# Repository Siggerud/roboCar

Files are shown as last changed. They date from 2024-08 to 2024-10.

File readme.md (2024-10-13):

# Robocar
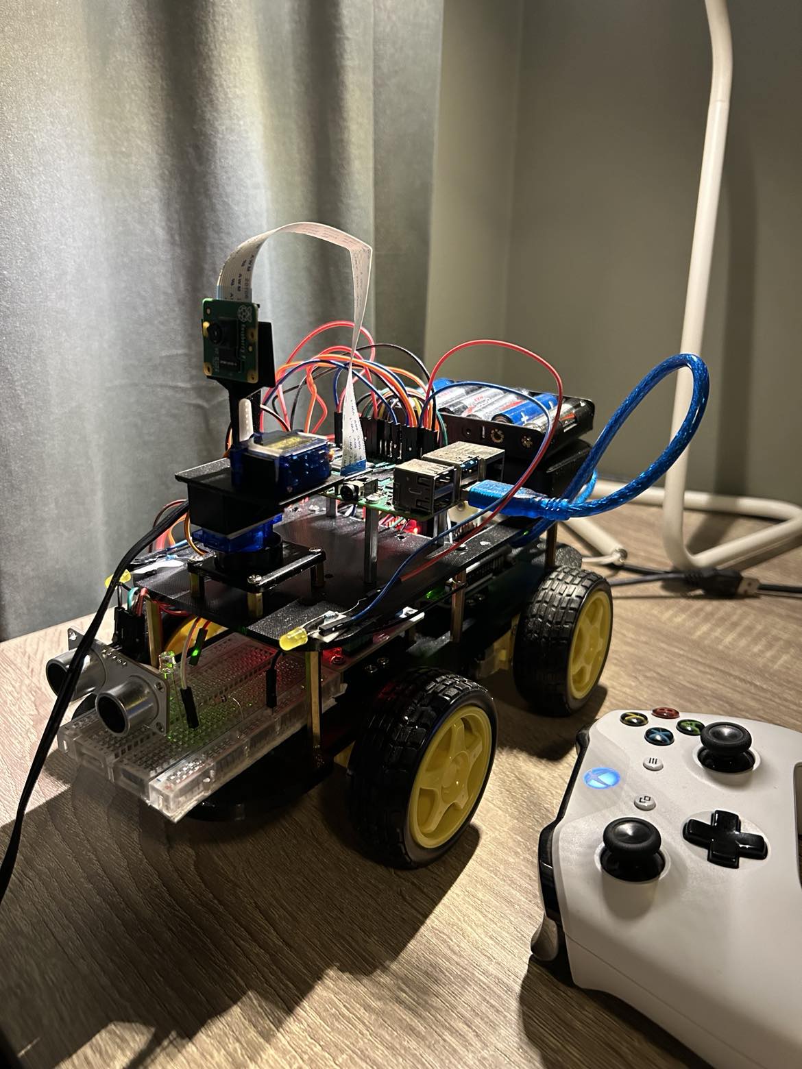
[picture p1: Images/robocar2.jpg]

The robocar with Xbox controller
#Todo: add updated picture
<br />
<br />
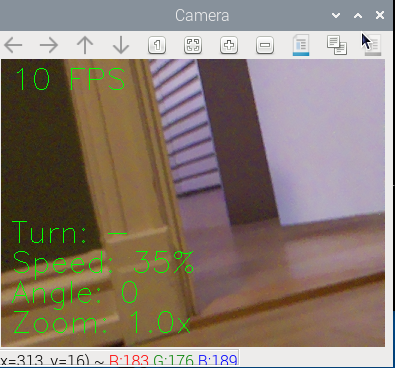
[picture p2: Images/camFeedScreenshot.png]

<br />
Camera feed screenshot from camera onboard robocar

This is a project where I've built
a vehicle that can be controlled with a wireless xbox controller via bluetooth.
It has a camera mounted on a servo that can be turned left and right, and it can be tilted back- and
forward.
It also has a distance sensors in the front and the back of the car, and a warning sound will
be set off if the vehicle is too close to any object. The closer the car is 
to an obstacle, the faster the alarm will beep. 
The front lights will dim according to the external lights, by reading data from a phototransistor.
I've used a serial connection to an arduino to read data from the distance sensors and the
phototransistor.

## Prerequisites

### Pairing you XBox controller
Pair your xBox One controller to your raspberry pi according to this [tutorial](https://pimylifeup.com/xbox-controllers-raspberry-pi/).

### Setting up remote connection
1. Enable your VNC connection by first opening the configuration settings
```
sudo raspi config
```
Enable Interface options -> VNC Enable

2. Find your ip adress for your raspberry pi
```
ifconfig
```
Look under wlan0 and find the adress after inet.

3. Download and install [RealVnc](https://www.realvnc.com/en/connect/download/combined/) for your OS.
Use the ip adress you found earlier to connect to your raspberry pi. Your pi needs to
be on the same network as the station you are connecting to it remotely from.

### Downloading necessary libraries
Due to some versions of libraries that might not work
correctly together when installed through pip, we need to use
sudo apt for some of the libraries instead 

```
sudo apt install -y libcamera-apps libcamera-dev libatlas-base-dev python3-kms++ python3-libcamera python3-pyqt5 python3-prctl
sudo apt install -y libhdf5-dev libhdf5-103 libjpeg-dev libjasper-dev

pip3 install picamera2
pip3 install pygame
pip3 install opencv-python
pip3 install pyserial
```

### Setting up pigpio
We need pigpio to control our servo, otherwise
there will be a lot of jitter.
```
sudo apt-get install pigpio 
sudo apt-get install  python-pigpio python3-pigpio
```

Setup pipgio service to run at boot
```
sudo systemctl enable pigpiod
```

Then reboot or start pipgio
```
sudo systemctl start pigpiod
```

### Upload code to arduino
1. Connect the Arduino Uno to your computer via USB cable
2. Download and install [Arduino IDE](https://www.arduino.cc/en/software).
3. Open the Arduino IDE
4. Go to files and open SerialComm.ino from this project
5. Under Tools -> Boards choose Arduino Uno
6. Under Tools -> Port choose the port that has Arduino Uno in paranthesis in the name
7. Press the upload button
8. Disconnect the Arduino Uno from the PC

### Add changes to config file if necessary
All user tweaking will be done in the config file. Here you can add or remove
components installed on the car, change pin numbers and other limit values for the car
1. Turn off any components you have not added to the car under Components.enabled
2. Change any pin connections that are deviating from the wiring list given below
3. Add or remove progressive lights if need be

## Starting up the program
1. Power your xbox controller and wait for it to connect to the pi
2. Connect to your pi via RealVNC
3. Open this project in a terminal 
4. Run main.py

## Driving and controlling the car
To drive the car:<br />
RT - Gas
LT - Reverse
D-Pad - Turn

If you stand still while turning, the wheels will turn opposite of the
adjacent side to turn faster.

To turn the camera:<br />
Use the RSB stick to turn the camera to the left and right. Letting the stick
go will make the camera go to the neutral position.

To zoom:<br />
Use the LSB stick to zoom in and out. Letting the stick go will set the zoom to
1x.

### Exiting the program
1. When you're finished press Ctrl+C or double tap the specified controller exit button to exit the program in a controlled manner
2. Power off your xBox controller

### Running tests
To make sure everything is as expected you can run some
tests written to verify the classes in this project. To test
you just have to run the test files.

## Appendix

### Wiring
#### Raspberry Pi to L289
22 -> IN2 <br />
18 -> IN1 <br />
16 -> IN4 <br />
15 -> IN3 <br />
11 -> ENA <br />
13 -> ENB <br /> 
GND -> GND

#### Raspberry pi to horizontal servo
37 -> SignalWire <br />
3.3V -> + <br />
GND -> -

#### Raspberry pi to vertical servo
33 -> SignalWire <br />
3.3V -> + <br />
GND -> -

#### Raspberry pi to camera
Cameraslot -> Camera

#### Raspberry pi to arduino
USB-A -> USB-B

#### Raspberry pi to passive buzzer
29 -> +
GND -> -

#### Raspberry pi to LEDs
LED 1<br />
36 -> +
GND -> -
<br />
LED 2<br />
31 -> +
GND -> -

#### L289 to motors
L289 right and left should be based on looking at the
l289 from above reading the text. <br /> 

L289 MOTORA Left -> Right motor front + <br /> 
L289 MOTORA Left -> Right motor back + <br /> 
L289 MOTORA Right -> Right motor back - <br /> 
L289 MOTORA Right -> Right motor front - <br /> 

L289 MOTORB Right -> Left motor front + <br /> 
L289 MOTORB Right -> Left motor back + <br /> 
L289 MOTORB Left -> Left motor back - <br /> 
L289 MOTORB Left -> Left motor front - <br />

#### L289 to batterypack
L289 VMS -> Batterypack +-<br />
L289 GND -> Batterypack -

#### Arduino to front distance sensor
A2 -> Echo <br />
A3 -> Trig <br />
5V -> + <br />
GND -> -

#### Arduino to back distance sensor
A0 -> Echo <br />
A1 -> Trig <br />
5V -> + <br />
GND -> -

#### Arduino to phototransistor
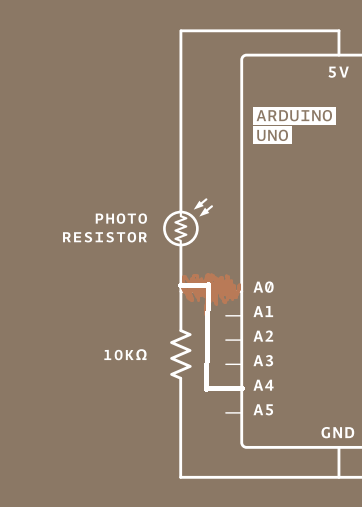
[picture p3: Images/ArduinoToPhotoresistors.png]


### Parts list

#### Car handling
Battery pack holding 6AA batteries <br />
4 TT motors <br />
L289N motor driver <br />
4 wheels that attach to motors <br />

#### Sensors
2 HC-SR04 distance sensors <br />
Photoresistor

#### Other electrical components
Raspberry Pi 4 model B <br />
Raspberry pi Camera Module V2 <br />
Powerbank 10000mah <br />
Arduino Uno <br />
Arduino Sensor Shield V5.0 <br />
2 SG90 servos <br />
Passive buzzer <br />
Breadboard <br />
2 yellow LED lights <br />
1 10K Ohm resistor <br />
2 220 Ohm resistor

#### Structural components
3D printed parts <br />
6x M3 40 mm spacers <br />
12x M3 10 mm spacers <br />
4 metal brackets for motors <br />
M3 screws
M3 nuts
female to female wires
male to female wires

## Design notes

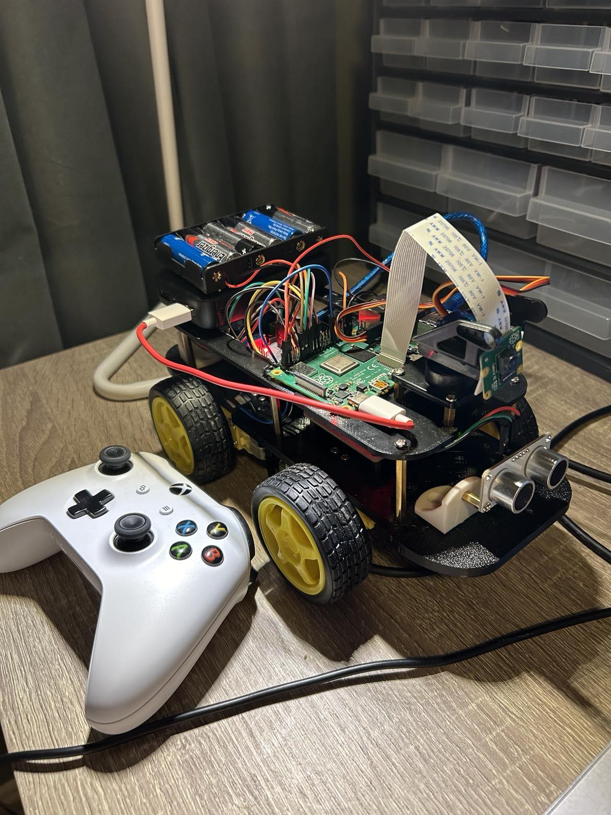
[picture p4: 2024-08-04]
Images/robocar.jpg

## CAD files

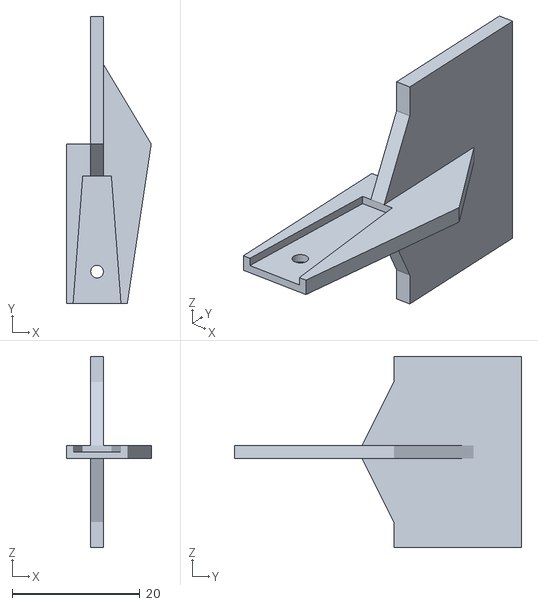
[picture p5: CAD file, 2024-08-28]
3D-files/Camera holder.stl
13.2 x 45.0 x 30.0

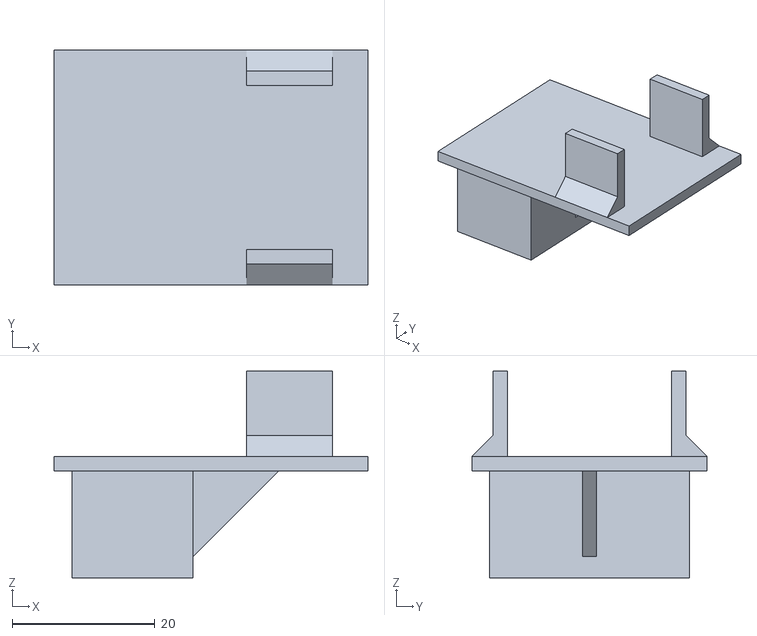
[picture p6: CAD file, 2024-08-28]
3D-files/Servo box.stl
44.0 x 33.0 x 29.0

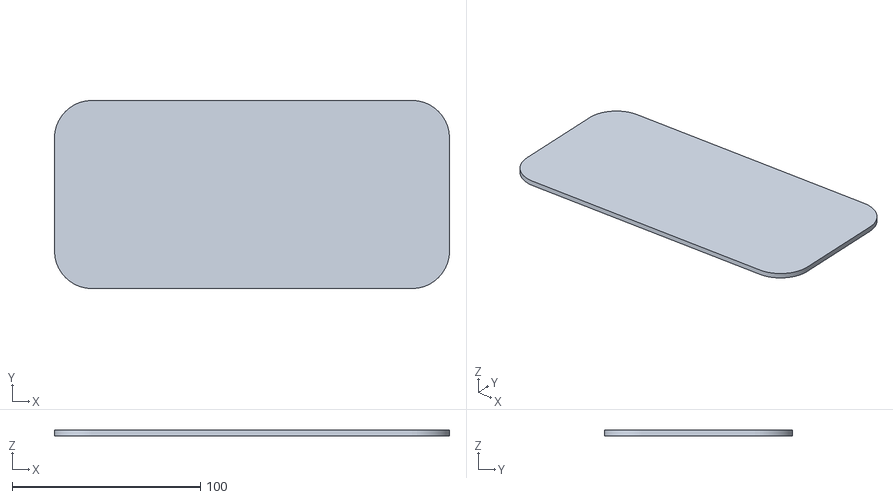
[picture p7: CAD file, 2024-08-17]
3D-files/Upper_part_chassis.stl
210.0 x 100.0 x 3.00

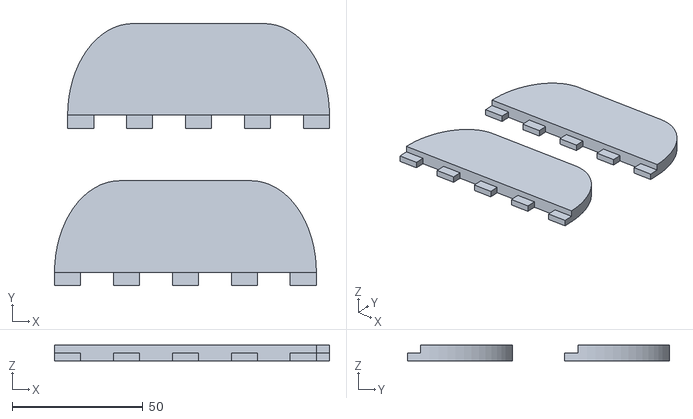
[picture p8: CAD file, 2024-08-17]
3D-files/Chassis ends.stl
105.0 x 100.0 x 6.00

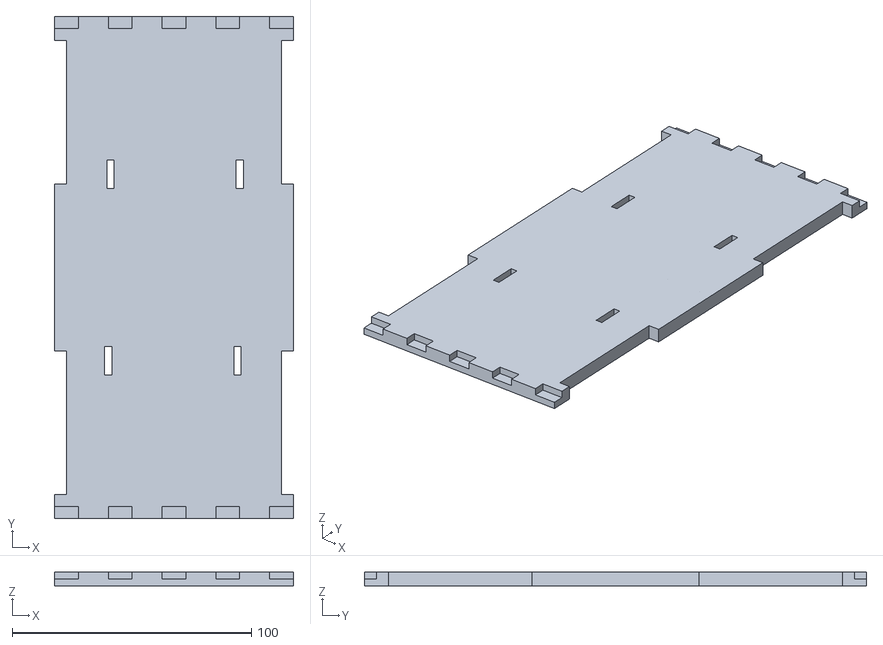
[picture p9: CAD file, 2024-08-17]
3D-files/Lower chassis Part 2.stl
100.0 x 210.0 x 6.00

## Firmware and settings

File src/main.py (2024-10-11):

from carHandling import CarHandling
from arduinoCommunicator import ArduinoCommunicator, InvalidPortError
from camera import Camera
from cameraHelper import CameraHelper
from servoHandling import ServoHandling
from carControl import CarControl, X11ForwardingError
from xboxControl import NoControllerDetected
from roboCarHelper import print_startup_error, convert_from_board_number_to_bcm_number
from time import sleep
from configparser import ConfigParser
import os

def setup_camera(parser):
    if not parser["Components.enabled"].getboolean("Camera"):
        return None

    cameraSpecs = parser["Camera.specs"]

    resolutionWidth = cameraSpecs.getint("ResolutionWidth")
    resolutionHeight = cameraSpecs.getint("ResolutionHeight")

    resolution = (resolutionWidth, resolutionHeight)
    camera = Camera(resolution)

    return camera


def setup_arduino_communicator(parser):
    if not parser["Components.enabled"].getboolean("ArduinoCommunicator"):
        return None

    arduinoCommunicatorData = parser["Arduino.specs"]

    port = arduinoCommunicatorData.get("Port")
    baudrate = arduinoCommunicatorData.getint("Baudrate", 9600)

    try:
        arduinoCommunicator = ArduinoCommunicator(port, baudrate)
    except InvalidPortError as e:
        print_startup_error(e)
        exit()

    buzzerPin = parser["Distance.buzzer.pin"].getint("Buzzer")

    if parser["Components.enabled"].getboolean("DistanceBuzzer"):
        arduinoCommunicator.activate_distance_sensors(buzzerPin)

    if parser["Components.enabled"].getboolean("ProgressiveLights"):
        progressiveLightPins = []
        lightPins = parser["Progressive.light.pins"]
        for key in lightPins:
            progressiveLightPins.append(lightPins.getint(key))

        arduinoCommunicator.activate_photocell_lights(progressiveLightPins)

    return arduinoCommunicator


def setup_servo(parser, plane):
    if plane == "horizontal":
        if not parser["Components.enabled"].getboolean("ServoHorizontal"):
            return None
    elif plane == "vertical":
        if not parser["Components.enabled"].getboolean("ServoVertical"):
            return None

    servoData = parser[f"Servo.handling.specs.{plane}"]

    servoPin = servoData.getint("ServoPin")
    minAngle = servoData.getint("MinAngle")
    maxAngle = servoData.getint("MaxAngle")

    servoPin = servoPin
    servoPin = convert_from_board_number_to_bcm_number(servoPin)

    servo = ServoHandling(
        servoPin,
        plane,
        minAngle,
        maxAngle
    )

    return servo


def setup_car(parser):
    if not parser["Components.enabled"].getboolean("CarHandling"):
        return None

    carHandlingPins = parser["Car.handling.pins"]

    # define GPIO pins
    rightForward = carHandlingPins.getint("RightForward")
    rightBackward = carHandlingPins.getint("RightBackward")
    leftForward = carHandlingPins.getint("LeftForward")
    leftBackward = carHandlingPins.getint("LeftBackward")
    enA = carHandlingPins.getint("EnA")
    enB = carHandlingPins.getint("EnB")
    minPwmTT = carHandlingPins.getint("MinimumMotorPWM")
    maxPwmTT = carHandlingPins.getint("MaximumMotorPWM")

    # define car handling
    car = CarHandling(
        leftBackward,
        leftForward,
        rightBackward,
        rightForward,
        enA,
        enB,
        minPwmTT,
        maxPwmTT
    )

    return car


# set up parser to read input values
parser = ConfigParser()
parser.read(os.path.join(os.path.dirname(__file__), 'config.ini'))

# set up car controller
try:
    carController = CarControl()
except (X11ForwardingError, NoControllerDetected) as e:
    print_startup_error(e)
    exit()

car = setup_car(parser)

arduinoCommunicator = setup_arduino_communicator(parser)

# define servos aboard car
servoHorizontal = setup_servo(parser, "horizontal")
servoVertical = setup_servo(parser, "vertical")

# setup camera
camera = setup_camera(parser)

# add components
if car:
    carController.add_car(car)
if servoHorizontal:
    carController.add_servo(servoHorizontal)

if servoVertical:
    carController.add_servo(servoVertical)

if arduinoCommunicator:
    carController.add_arduino_communicator(arduinoCommunicator)

if camera:
    cameraHelper = CameraHelper()
    cameraHelper.add_car(car)
    cameraHelper.add_servo(servoHorizontal)

    carController.add_camera(camera)
    carController.add_camera_helper(cameraHelper)

# start car
carController.start()

flag = carController.shared_flag

# keep process running until keyboard interrupt
try:
    while not flag.value:  # listen for any processes setting the event
        sleep(0.5)
except KeyboardInterrupt:
    flag.value = True # set event to stop all active processes
finally:
    print("finished!")

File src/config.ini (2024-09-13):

[Components.enabled]
CarHandling = true
ServoHorizontal = true
ServoVertical = true
ArduinoCommunicator = true
DistanceBuzzer = true
ProgressiveLights = true
Camera = true

[Car.handling.pins]
# IN2
RightForward = 22
# IN1
RightBackward = 18
# IN4
LeftForward = 16
# IN3
LeftBackward = 15
EnA = 11
EnB = 13
# This should be where the motor starts to "bite"
MinimumMotorPWM = 20
MaximumMotorPWM  = 60

[Servo.handling.specs.horizontal]
ServoPin = 37
MinAngle = -90
MaxAngle = 90

[Servo.handling.specs.vertical]
ServoPin = 33
MinAngle = -60
MaxAngle = 60

[Distance.buzzer.pin]
Buzzer = 29

# add more lights if needed
[Progressive.light.pins]
LightPin1 = 36
LightPin2 = 31

[Arduino.specs]
Port = /dev/ttyACM0
Baudrate = 115200

[Camera.specs]
ResolutionWidth = 384
ResolutionHeight = 288

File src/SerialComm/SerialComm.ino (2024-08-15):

//variables for back sensor
boolean sendDistanceBack = false;
const int inputPinBack = A0; // define ultrasonic receive pin (Echo)
const int outputPinBack = A1; // define ultrasonic send pin(Trig)

//variables for front sensor
boolean sendDistanceFront = false;
const int inputPinFront = A2; // define ultrasonic receive pin (Echo)
const int outputPinFront = A3; // define ultrasonic send pin(Trig)

//variables for photocell
boolean sendPhotocell = false;
const int inputPinPhotocell = A4;

const long baudrate = 115200; // the highest speed a pi can communicate with an arduino

void setup() {
  //set pin modes
  pinMode(inputPinBack, INPUT);
  pinMode(outputPinBack, OUTPUT);

  pinMode(inputPinFront, INPUT);
  pinMode(outputPinFront, OUTPUT);

  pinMode(inputPinPhotocell, INPUT);

  //start serial communication
  Serial.begin(baudrate);
}

void loop() {
  //listen for incoming commands from pi
  listen_for_commands();

  // write sensor values to pi
  if (sendDistanceBack) {
    write_distance_to_serial(inputPinBack, outputPinBack);
  } else if (sendDistanceFront) {
    write_distance_to_serial(inputPinFront, outputPinFront);
  } else if (sendPhotocell) {
    write_photocell_value_to_serial(inputPinPhotocell);
  }

  //reset boolean values
  sendDistanceBack = false;
  sendDistanceFront = false;
  sendPhotocell = false;
}

void listen_for_commands() {
  if (Serial.available()){ // check if there is incoming data over the serial port
    String command = Serial.readStringUntil('\n'); //command from raspberry pi
    if (command == "back"){
      sendDistanceBack = true;
    } else if (command == "front"){
      sendDistanceFront = true;
    } else if (command == "photocell"){
      sendPhotocell = true;
    }
  }
}

void write_distance_to_serial(int inputPin, int outputPin) {
  digitalWrite(outputPin, LOW); //send no signal
  delayMicroseconds(2); // wait 2 microseconds
  digitalWrite(outputPin, HIGH); //send signal for 10 microseconds
  delayMicroseconds(10); 
  digitalWrite(outputPin, LOW); //turn off signal
  float distance = pulseIn(inputPin, HIGH); //get distance by listening for signal
  distance= distance/5.8/10;

  Serial.println(String(distance)); //sending data
}

void write_photocell_value_to_serial(int inputPin) {
  int photocellValue = analogRead(inputPinPhotocell);

  Serial.println(String(photocellValue));
}

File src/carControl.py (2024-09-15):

import subprocess
from multiprocessing import Process, Array, Value
from xboxControl import XboxControl
from time import sleep

class CarControl:
    def __init__(self):
        if not self._check_if_X11_connected():
            raise X11ForwardingError("X11 forwarding not detected.")

        self._xboxControl = XboxControl()

        self._car = None
        self._servoEnabled = False
        self._servos = []
        self._arduinoCommunicator = None

        self._camera = None
        self._cameraHelper = None

        self._processes = []

        self._buttonToObjectDict = {
        }

        self.shared_array = None
        self.shared_flag = Value('b', False)

    def add_arduino_communicator(self, arduinoCommunicator):
        self._arduinoCommunicator = arduinoCommunicator

    def add_car(self, car):
        self._car = car

    def add_camera(self, camera):
        self._camera = camera

    def add_camera_helper(self, cameraHelper):
        self._cameraHelper = cameraHelper

    def add_servo(self, servo):
        self._servos.append(servo)
        if not self._servoEnabled:
            self._servoEnabled = True

    def start(self):
        if self._camera:
            self._get_camera_ready() # this needs to be first method called

            self._activate_camera()

        if self._arduinoCommunicator:
            self._activate_arduino_communication()

        self._activate_car_handling()

    def cleanup(self):
        # close all threads
        for process in self._processes:
            process.join()

    def _get_camera_ready(self):
        self._set_shared_array_and_array_dict()

        if self._car:
            self._camera.set_car_enabled()

        if self._servoEnabled:
            self._camera.set_servo_enabled()

    def _set_shared_array_and_array_dict(self):
        arrayInput = []
        arrayDict = {}
        counter = 0
        if self._car:
            arrayDict["speed"] = counter
            arrayInput.append(0.0)
            counter += 1

            arrayDict["turn"] = counter
            arrayInput.append(0.0)
            counter += 1

        if self._servoEnabled:
            arrayDict["servo"] = counter
            arrayInput.append(0.0)
            counter += 1

        arrayDict["HUD"] = counter
        arrayInput.append(0.0)
        counter += 1

        arrayDict["Zoom"] = counter
        arrayInput.append(1.0)

        self.shared_array = Array('d', arrayInput)

        self._camera.add_array_dict(arrayDict)
        self._cameraHelper.add_array_dict(arrayDict)


    def _activate_camera(self):
        process = Process(target=self._start_camera, args=(self.shared_array, self.shared_flag))
        self._processes.append(process)
        process.start()

    def _activate_arduino_communication(self):
        process = Process(target=self._start_listening_for_arduino_communication, args=(self.shared_flag,))
        self._processes.append(process)
        process.start()

    def _activate_car_handling(self):
        process = Process(target=self._start_listening_for_xbox_commands, args=(self.shared_array, self.shared_flag))
        self._processes.append(process)
        process.start()

    def _start_listening_for_xbox_commands(self, shared_array, flag):
        self._print_button_explanation()
        self._map_all_objects_to_buttons()

        if self._car:
            self._car.setup()

        if self._servoEnabled:
            for servo in self._servos:
                servo.setup()

        while not flag.value:
            for event in self._xboxControl.get_controller_events():
                button, pressValue = self._xboxControl.get_button_and_press_value_from_event(event)
                if self._xboxControl.check_for_exit_event(button):
                    self._exit_program(flag)
                    break

                # get the object to take action based on the button pushed
                try:
                    self._buttonToObjectDict[button].handle_xbox_input(button, pressValue)
                except KeyError: # if key does not correspond to object, then go to next event
                    continue

                if self._cameraHelper:
                    self._cameraHelper.update_control_values_for_video_feed(shared_array)

        if self._car:
            self._car.cleanup()

        if self._servoEnabled:
            for servo in self._servos:
                servo.cleanup()

        self._xboxControl.cleanup()

        print("Exiting car handling")

    def _start_camera(self, shared_array, flag):
        self._camera.setup()

        while not flag.value:
            self._camera.show_camera_feed(shared_array)

        self._camera.cleanup()

    def _start_listening_for_arduino_communication(self, flag):
        self._arduinoCommunicator.setup()

        while not flag.value:
            # start the communicator
            self._arduinoCommunicator.start()
            sleep(0.01)  # sleep too not use too much CPU resources

        # cleanup when flag is set to true
        self._arduinoCommunicator.cleanup()
        print("Exiting arduino")

    def _print_button_explanation(self):
        print()
        print("Controller layout: ")
        if self._car:
            print("Car controls:")
            print("Turn left: " + self._car.get_car_buttons()["Left"])
            print("Turn right: " + self._car.get_car_buttons()["Right"])
            print("Drive forward: " + self._car.get_car_buttons()["Gas"])
            print("Reverse: " + self._car.get_car_buttons()["Reverse"])
            print()
        if self._servoEnabled:
            print("Servo controls:")
            for servo in self._servos:
                print("Turn servo" + servo.get_plane() + ": " + servo.get_servo_buttons()["Servo"])
            print()
        if self._camera:
            print("Camera controls")
            print("Zoom camera: " + self._cameraHelper.get_camera_buttons()["Zoom"])
            print("Turn HUD on or off: " + self._cameraHelper.get_camera_buttons()["HUD"])
            print()

        print(f"Double tap {self._xboxControl.get_exit_button()} to exit")

    def _map_all_objects_to_buttons(self):
        if self._car:
            self._add_object_to_buttons(self._car.get_car_buttons(), self._car)

        if self._servoEnabled:
            for servo in self._servos:
                self._add_object_to_buttons(servo.get_servo_buttons(), servo)

        if self._cameraHelper:
            self._add_object_to_buttons(self._cameraHelper.get_camera_buttons(), self._cameraHelper)

    def _add_object_to_buttons(self, buttonDict, roboObject):
        for button in list(buttonDict.values()):
            self._buttonToObjectDict[button] = roboObject

    def _exit_program(self, flag):
        flag.value = True
        print("Exiting program...")
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

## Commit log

2024-06-12 added steering functionality
2024-06-16 added steering without gas
2024-06-16 added pwm treshold
2024-06-17 added stationary steering
2024-06-17 stationary steering fix
2024-06-17 added thread
2024-06-17 testing thread event
2024-06-21 changed pin placements
2024-06-21 added comments for pin placements
2024-06-22 added handling of arduino not being connected
2024-06-24 added servo handling
2024-06-24 print line
2024-06-29 changed order of servo min and max values
2024-06-29 made camera class and added rotation
2024-06-29 added info print statement
2024-07-04 cleaned up code in Camera class
2024-07-04 added arduino file
2024-07-07 added two-way communication between arduino and raspberry pi
2024-07-07 updated arduino code
2024-07-10 added pipgio steering
2024-07-10 added own class for servo handling
2024-07-11 added printing of controller power level
2024-07-11 added new distance sensor class
2024-07-24 changed arduino file
2024-07-24 removed threading
2024-07-25 added threading to xboxControl class
2024-07-25 added threading to xbox control class
2024-07-25 moved all threading logic to DistanceWarner
2024-07-25 rewrote variable names in arduino script
2024-07-25 added a method for ending threads in xboxControl
2024-07-31 added text to frames
2024-07-31 added servo text
2024-08-01 set initial value for servo to be 0 degrees
2024-08-04 changed logic for displaying control values on camera feed
2024-08-05 added printing of xbox control layout
2024-08-10 added test file for servo
2024-08-10 added servo asserts
2024-08-11 added new thread for camera operation
2024-08-15 added wiring information to readme
2024-08-15 rewrote arduino communication structure
2024-08-17 added 3D files
    [Chassis ends.stl, Lower chassis Part 2.stl, Upper_part_chassis.stl]
2024-08-27 refactored code to allow multiple servos
2024-08-28 added 3D files and updated readme
    [Camera holder.stl, Servo box.stl]
2024-09-28 small changes to picam2 setup in camera
2024-09-28 made test file for camera
2024-09-29 added tests for Camera class
2024-09-30 finished tests for camera
2024-10-05 finished tests on Honker and added testfile for ArduinoCommunicator
2024-10-06 finished tests for ArduinoCommunicator and changed some logic in the start method
2024-10-27 added print statement
2024-10-27 removed print statement
